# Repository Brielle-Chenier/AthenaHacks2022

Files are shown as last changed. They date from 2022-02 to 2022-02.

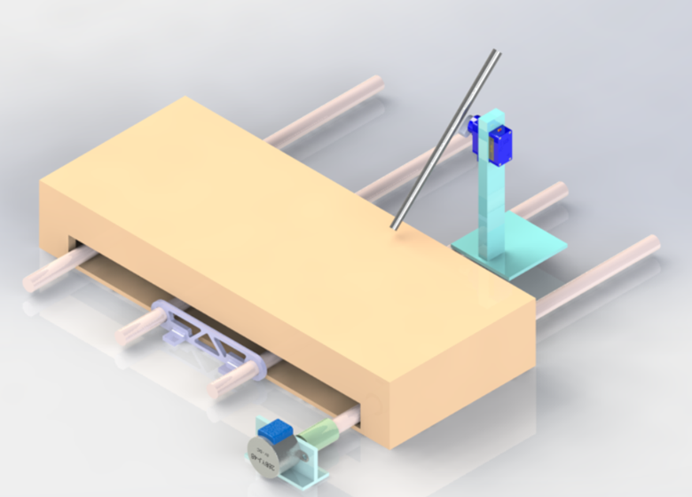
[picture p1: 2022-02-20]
CAD render.png

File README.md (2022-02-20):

Get Nailed

# AthenaHacks2022
Get Nailed

# Inspiration
We've all faced the struggle of painting our nails, especially our non-dominant hand.  Get Nailed solves effortless painting of both hands! It can even allow you to multitask while you wait to get your nails painted!

# What it does
Our project detects when a finger is placed, adjusts to the correct position, and paints the nail until all nails are complete. In between each nail, a conveyor under the table moves the brush to the nail paint where it can redip so each nail is fresh!

# How we built it
We built this project with Arduino, a few 3D printed parts, and lots of cardboard. The main parts of this project were the conveyor belt and the nail painting brush. The conveyor belt was made using 2 stepper motors, wooden dowels, and elastic bands to propagate the belt forward. The nail painter was made by mounting a servo motor to a wooden stick apparatus. The servo was attached to a paintbrush that can now mimic the flick motion used to paint a nail. The system is started by the presence of a finger on our finger painting station, we sense this with a capacitive touch sensor. An added feature is the LED animations that run in the box as your nail gets painted. 

# Challenges we ran into
One challenge we ran into was calibrating the right 'flick' motion to fully paint a nail. Another big issue was being able to get the conveyor belt to move. Many times it seemed the motors weren't strong enough, there wasn't enough tension, or the rubber bands would bunch up and stop the movement. The belt was super hard to get working consistently and required constant human intervention during the early stages of development. Some of the fixes we tried were different ways to attach the rubber bands to the dowels i.e. having one long rubber band go all the way over or having several smaller rubber bands attached in steps throughout. We also tried several solutions to get the sticks to stay straight in the middle to stop them from going wayward due to the tension. These included creating holders out of cardboard, clay moulds that would double as bearings, designing a Solidworks part that ended up being too long of a print, and our chosen solution of using smaller dowels to create little windows on the other side for the big dowels to sit in.

# Accomplishments that we're proud of
Being able to set up the machine in a way that it is able to successfully find the nail each time. Calibrating the machine was very challenging and due to the inconsistency in the belt, it had to be redone several times. Just being able to look at our final project with all the struggles and changes and thinking 'wow this actually works' is our biggest accomplishment.

# What we learned
We enjoyed putting our Arduino knowledge and to the test for this hack.  It was fun to learn how to work with the capacitive touch sensor and incorporate it into our design.  Although the mechanical debug of the machine was sometimes quite frustrating, it was a good challenge and we were satisfied with our solutions in the end.

# What's next for Get Nailed
We would love to make our project be able to rotate about a user's hand so that it can paint every nail without having to change your finger each time. We also want to add a fan to be able to dry your nails as well as an option to pick from different colors or even set a pattern.

CAD render

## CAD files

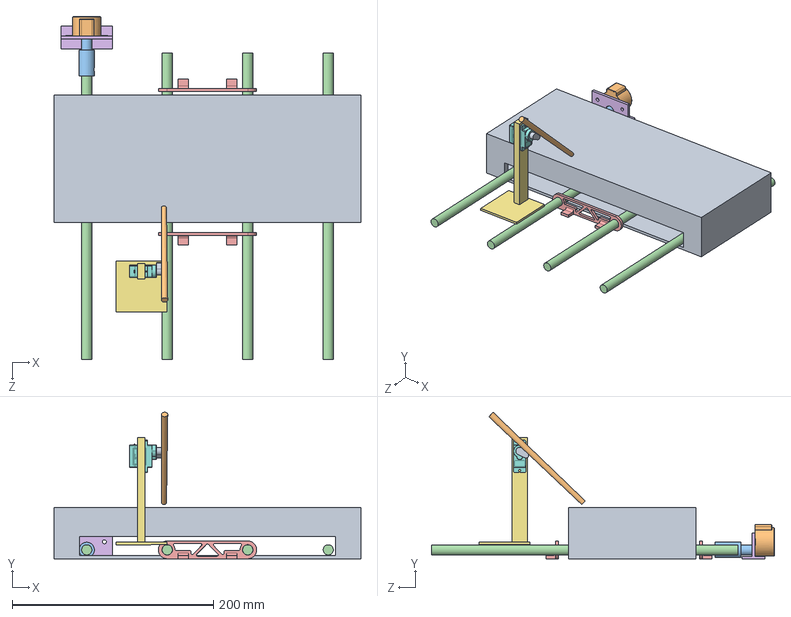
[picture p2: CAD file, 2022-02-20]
CAD/MainAssm.SLDASM
304.8 x 145.7 x 340.8 mm
Stepper_28BYJ48
StepperAdapter
Dowel x 4
DowelSideSpacer x 2
MotorMount
BrushBase
SG90 Servo.step
ServoAdapter
paintBrush

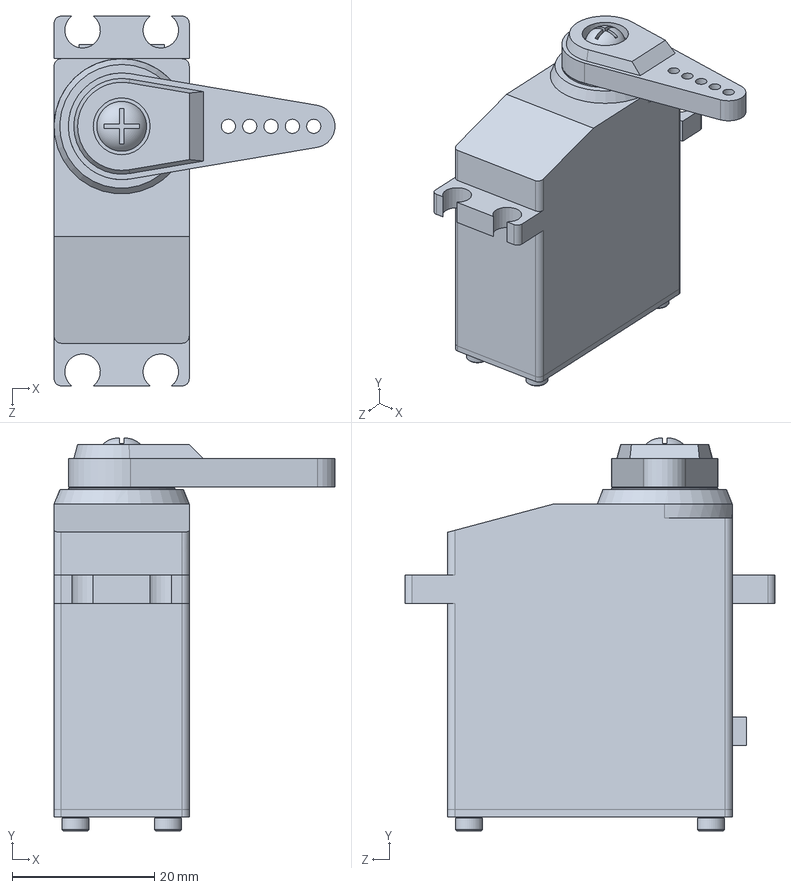
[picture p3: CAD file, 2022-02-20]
CAD/sevo.SLDPRT
39.5 x 55.2 x 52.0 mm

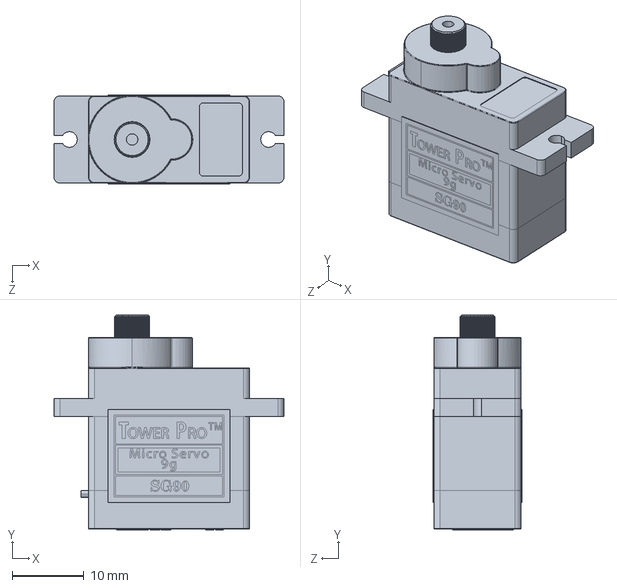
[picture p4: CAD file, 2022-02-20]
CAD/SG90 Servo.step.SLDPRT
32.1 x 30.0 x 12.4 mm

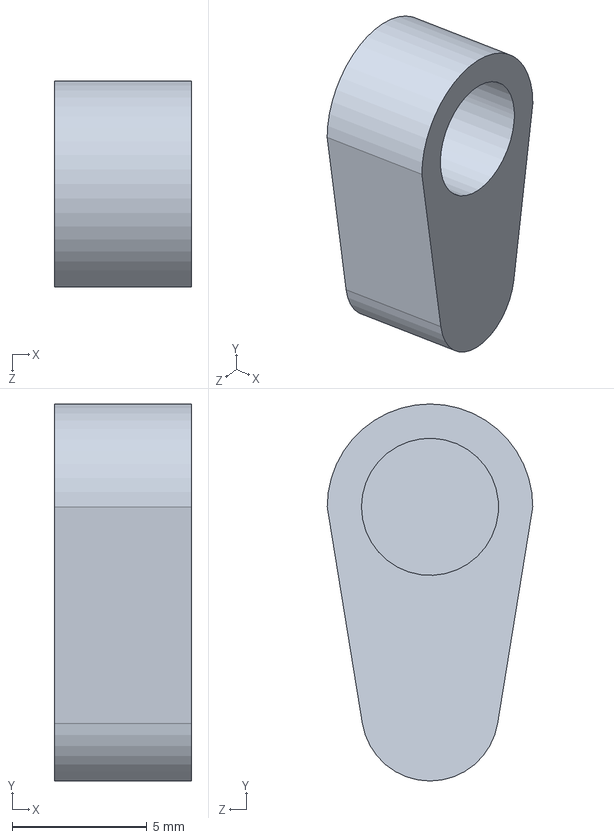
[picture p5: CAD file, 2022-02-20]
CAD/ServoAdapter.SLDPRT
5.08 x 14.0 x 7.62 mm

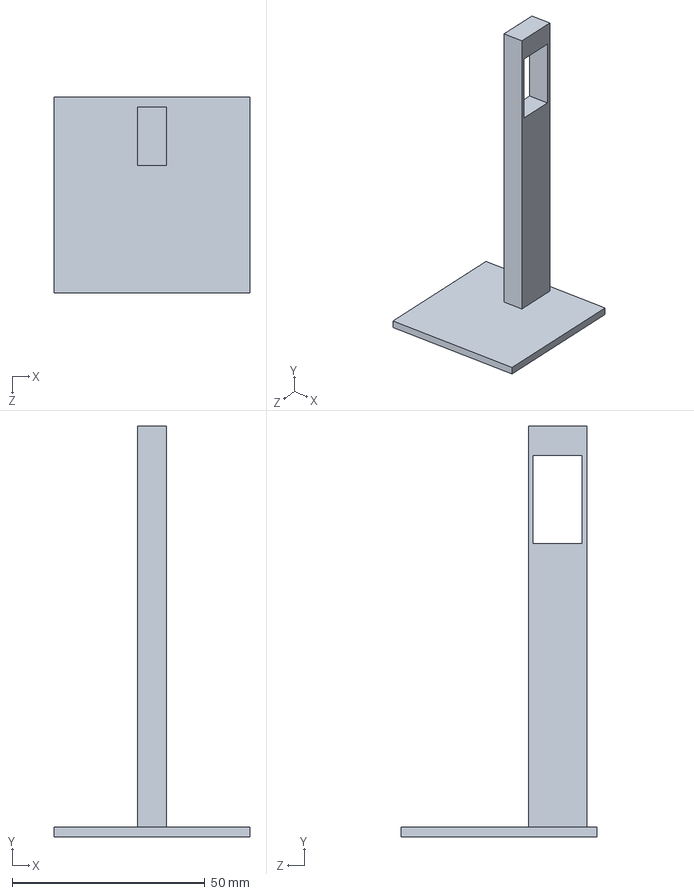
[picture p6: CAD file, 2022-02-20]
CAD/BrushBase.SLDPRT
50.8 x 106.7 x 50.8 mm

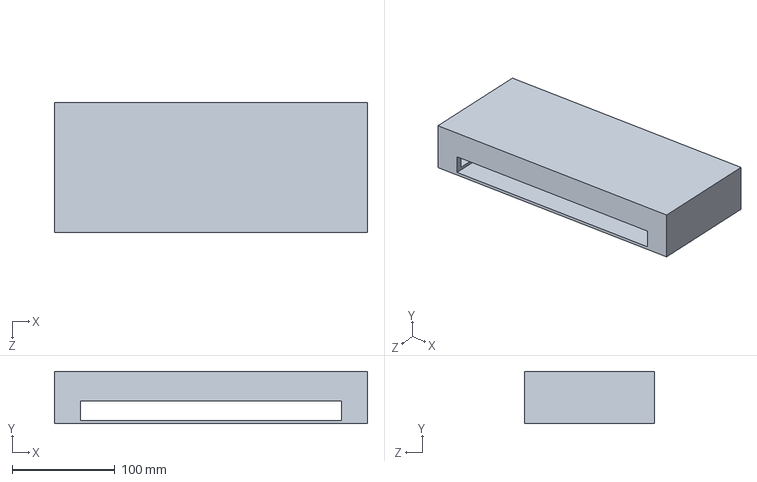
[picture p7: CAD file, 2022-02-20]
CAD/Box.SLDPRT
304.8 x 50.8 x 127.0 mm

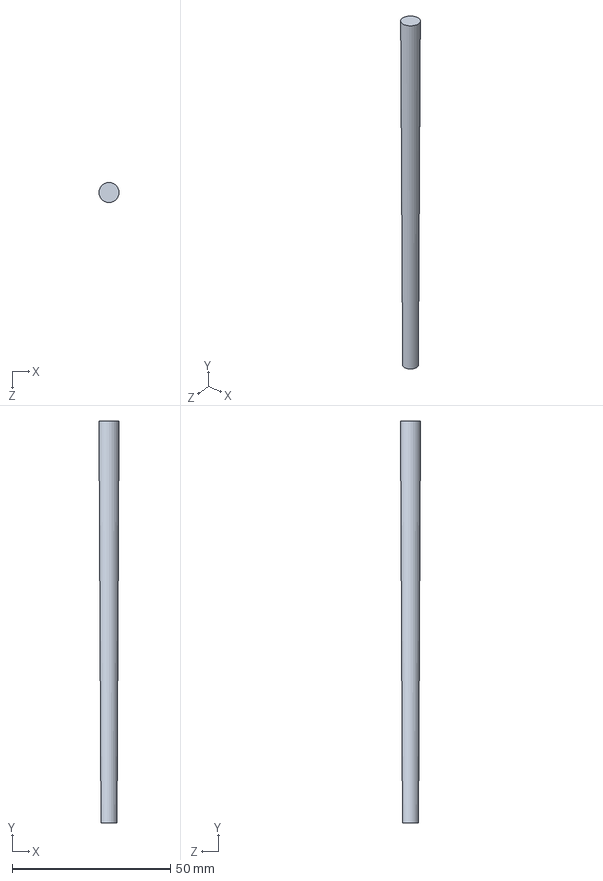
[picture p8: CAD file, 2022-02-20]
CAD/paintBrush.SLDPRT
6.35 x 127.0 x 6.35 mm

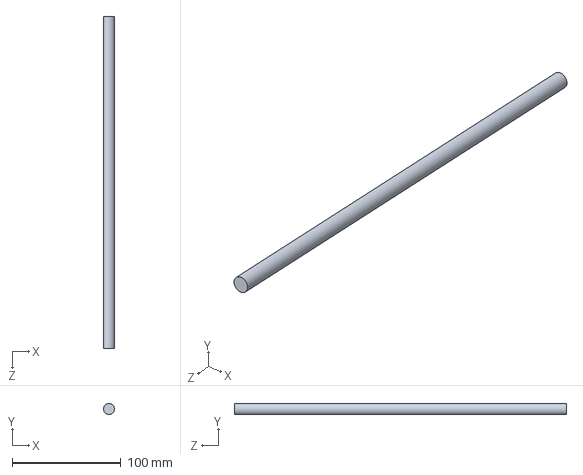
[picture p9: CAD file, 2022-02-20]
CAD/Dowel.SLDPRT
10.2 x 10.2 x 304.8 mm

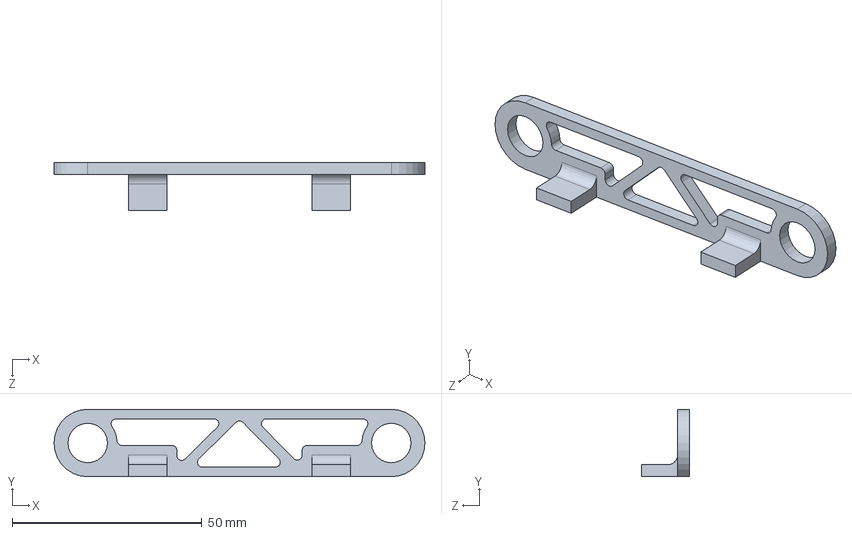
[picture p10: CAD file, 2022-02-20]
CAD/DowelSideSpacer.SLDPRT
97.8 x 17.8 x 12.7 mm

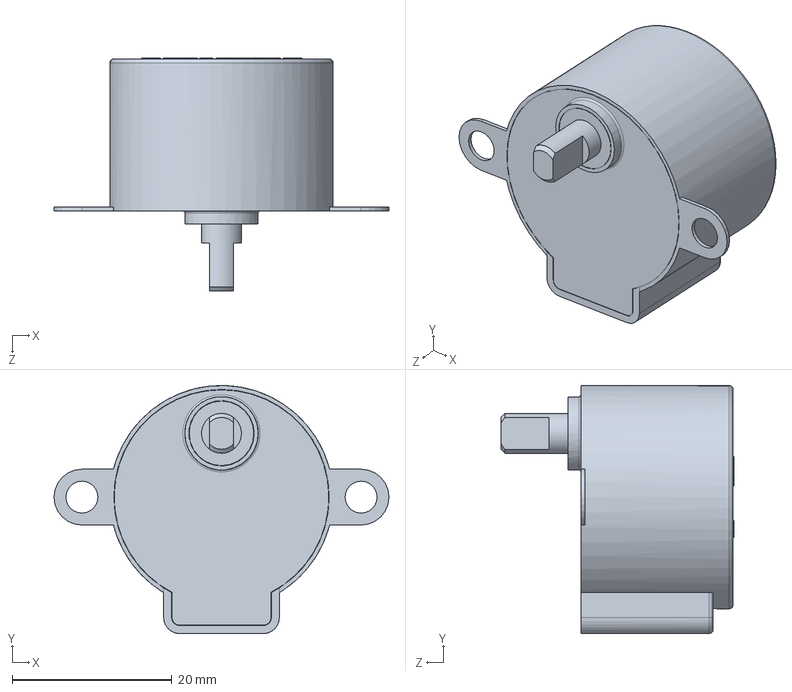
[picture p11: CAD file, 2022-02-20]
CAD/Stepper_28BYJ48.SLDPRT
42.0 x 31.1 x 29.2 mm

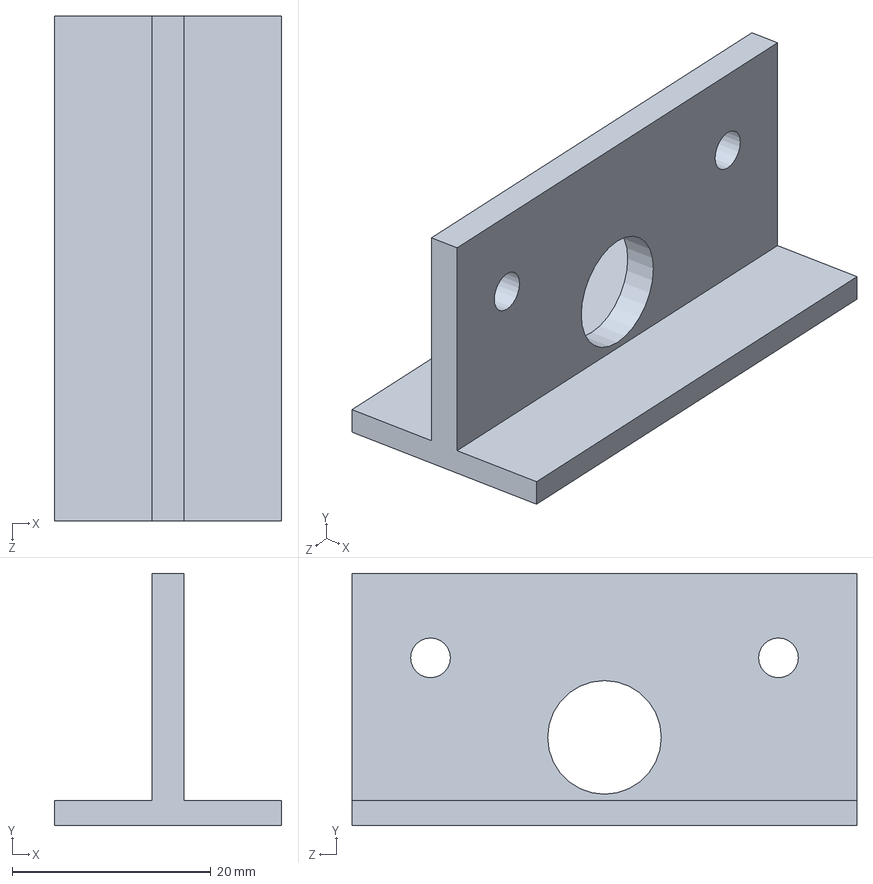
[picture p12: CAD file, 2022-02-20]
CAD/MotorMount.SLDPRT
22.9 x 25.4 x 50.8 mm

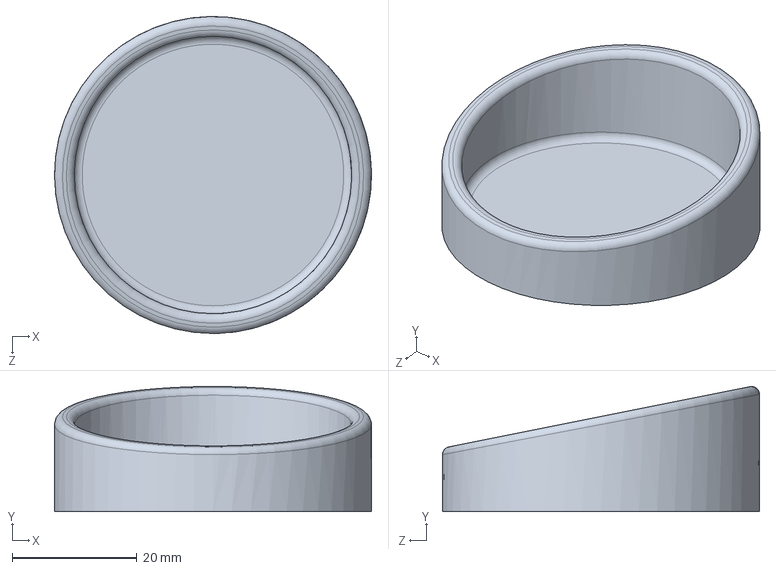
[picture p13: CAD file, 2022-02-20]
CAD/NailPolishBowl.SLDPRT
50.8 x 20.0 x 50.8 mm

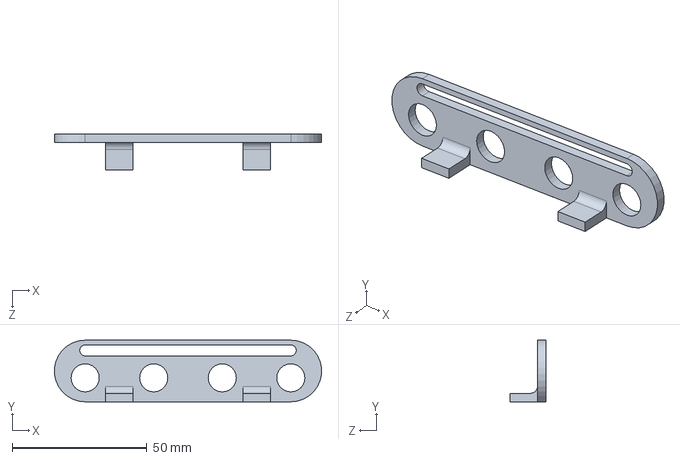
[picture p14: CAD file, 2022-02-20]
CAD/DowelSideSpacer2.SLDPRT
98.9 x 22.9 x 13.3 mm

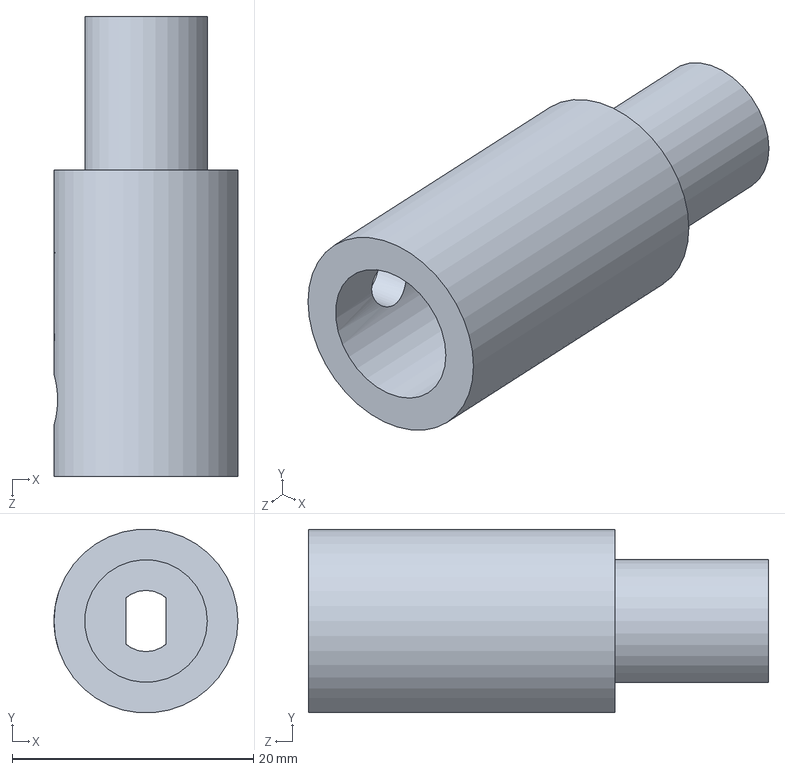
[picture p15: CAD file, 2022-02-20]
CAD/StepperAdapter.SLDPRT
15.2 x 15.2 x 38.1 mm

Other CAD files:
CAD/DowelSideSpacer.STL
CAD/DowelSideSpacer2.STL
CAD/NailPolishBowl.STL
CAD/StepperAdapter.STL

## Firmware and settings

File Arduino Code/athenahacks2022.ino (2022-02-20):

#include <Servo.h>
Servo servo1;

int servoPin = 9;
int touchPin = 8;
int count  = 0;
#define step_pin1 10
#define step_pin2 11
#define step_pin3 12
#define step_pin4 13
#define comm_pin 7
#define comm_pin2 4
int step_num = 0;
int initial = 20;

#include <FastLED.h>
//#include <PS2Keyboard.h>
#define LED_PIN 2
#define NUM_LED 36
#define CAP = 3
//#define DATA_PIN 8
//#define IRQ_PIN 5
#define ARRAY_SIZE(A) (sizeof(A)/sizeof((A)[0]))
CRGB leds[NUM_LED];

void setup() {
  // put your setup code here, to run once:
  servo1.attach(servoPin);
  servo1.write(initial);
  pinMode(touchPin, INPUT);
  pinMode(LED_BUILTIN, OUTPUT);
  pinMode(step_pin1, OUTPUT);
  pinMode(step_pin2, OUTPUT);
  pinMode(step_pin3, OUTPUT);
  pinMode(step_pin4, OUTPUT);
  digitalWrite(step_pin1,LOW);
  digitalWrite(step_pin2,LOW);
  digitalWrite(step_pin3,LOW);
  digitalWrite(step_pin4,LOW);
  pinMode(comm_pin, OUTPUT);
  digitalWrite(comm_pin,LOW);
  pinMode(comm_pin2, OUTPUT);
  digitalWrite(comm_pin2,LOW);
  delay(1000);
  FastLED.addLeds<WS2812B, LED_PIN, RGB>(leds, NUM_LED);
  FastLED.setMaxPowerInVoltsAndMilliamps(5, 500);
  FastLED.clear();
  done();
  FastLED.show();
  
}

typedef void (*SimplePatternList[])();
SimplePatternList PATTERNS = {painting, done};
int state = 0;
int chargeState = 0;

void loop() {
  // put your main code here, to run repeatedly:
  //7 degree dif
  //int brush = 10;
  
  if(digitalRead(touchPin) == HIGH and count == 0) {
    painting();
    servo1.write(10);
    delay(1000);
    servo1.write(10 + 10);
    delay(1000);
    servo1.write(initial);
    delay(100);
    digitalWrite(comm_pin, HIGH);
    delay(20);
    digitalWrite(comm_pin, LOW);
    stepRight(6200);
    count = 1;
    servo1.write(initial+25);
    delay(1000);
    servo1.write(initial - 15);
    delay(2000);
    servo1.write(initial+25);
    delay(1000);
    digitalWrite(comm_pin2, HIGH);
    delay(20);
    digitalWrite(comm_pin2, LOW);
    done();
    stepLeft(6200);
    
  }

  if(digitalRead(touchPin) == LOW)  {
    count = 0;
    servo1.write(initial);
  }
}

void stepRight(int step_number) {
  while(step_number>=0){
    switch(step_number%4){
      case 0:
      digitalWrite(step_pin1,HIGH);
      digitalWrite(step_pin2, LOW);
      digitalWrite(step_pin3,LOW);
      digitalWrite(step_pin4, LOW);
      break;
      case 1:
      digitalWrite(step_pin1,LOW);
      digitalWrite(step_pin2, HIGH);
      digitalWrite(step_pin3,LOW);
      digitalWrite(step_pin4, LOW);
      break;
      case 2:
      digitalWrite(step_pin1,LOW);
      digitalWrite(step_pin2, LOW);
      digitalWrite(step_pin3,HIGH);
      digitalWrite(step_pin4, LOW);
      break;
      case 3:
      digitalWrite(step_pin1,LOW);
      digitalWrite(step_pin2, LOW);
      digitalWrite(step_pin3,LOW);
      digitalWrite(step_pin4, HIGH);
      break;
    }
    step_number = step_number - 1;
    delay(2);
  }
}

void stepLeft(int step_number) {
  while(step_number>=0){
    switch(step_number%4){
      case 0:
      digitalWrite(step_pin1,LOW);
      digitalWrite(step_pin2, LOW);
      digitalWrite(step_pin3,LOW);
      digitalWrite(step_pin4, HIGH);
      break;
      case 1:
      digitalWrite(step_pin1,LOW);
      digitalWrite(step_pin2, LOW);
      digitalWrite(step_pin3,HIGH);
      digitalWrite(step_pin4, LOW);
      break;
      case 2:
      digitalWrite(step_pin1,LOW);
      digitalWrite(step_pin2, HIGH);
      digitalWrite(step_pin3,LOW);
      digitalWrite(step_pin4, LOW);
      break;
      case 3:
      digitalWrite(step_pin1,HIGH);
      digitalWrite(step_pin2, LOW);
      digitalWrite(step_pin3,LOW);
      digitalWrite(step_pin4, LOW);      
      break;
    }
    step_number = step_number - 1;
    delay(2);
  }
}

void painting ()
{
    for (int i = 0; i < NUM_LED; i++){
      leds[i]= CRGB(0,255,0);
    }
    FastLED.show();
}


void done ()
{
    for (int i = 0; i < NUM_LED; i++){
          leds[i]= CRGB(255,0,0);
    }
    FastLED.show();

}

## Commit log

2022-02-20 CAD files for project
    [BrushBase.SLDPRT, Dowel.SLDPRT, DowelSideSpacer.SLDPRT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]
2022-02-20 arduino code
    all done!
